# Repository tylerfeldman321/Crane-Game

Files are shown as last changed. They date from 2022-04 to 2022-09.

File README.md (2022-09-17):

<p align="center">
  
</p>

# Advanced Computer Architecture (ECE 350) Project - Crane Game
## Project Description
This is a project a partner and I built for an advanced computer architecture course. We incorporated a custom processor into a physical system we built to create a crane game where the user picks up boxes and drops them into a container to gain points. Our processor keeps track of the score and game logic while the rest of the system handles motors and sensors.

<p align="center">
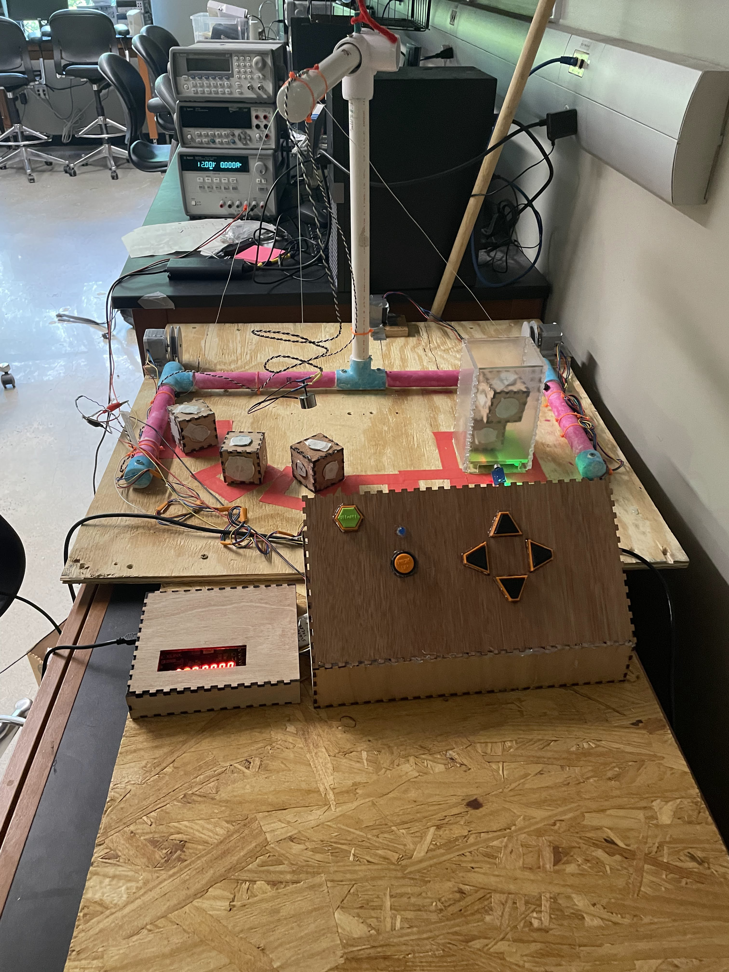
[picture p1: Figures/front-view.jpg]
  
</p>

## Game
The goal of the game is to pickup as many boxes from the playing field and drop them into a acrylic case before time runs out. Once the user presses the start button, time will start counting down from a amount configured in the code (1 minute as default). When the game is active, the user can use the controls to rotate a PVC crane left or right, and move an electromagnet up/down that is hanging off the boom of the crane. The user can click a button to toggle the electromagnet, allowing the crane to pick up the boxes in the playing field. They can then drop them into the acrylic case, gaining points. After the time runs out, the points are recorded and game stops.

Below is a birds-eye view of the game and playing area. The boxes are outlined with red tape, as is the acrylic case on the left, where the user is meant to drop the boxes.

<p align="center">
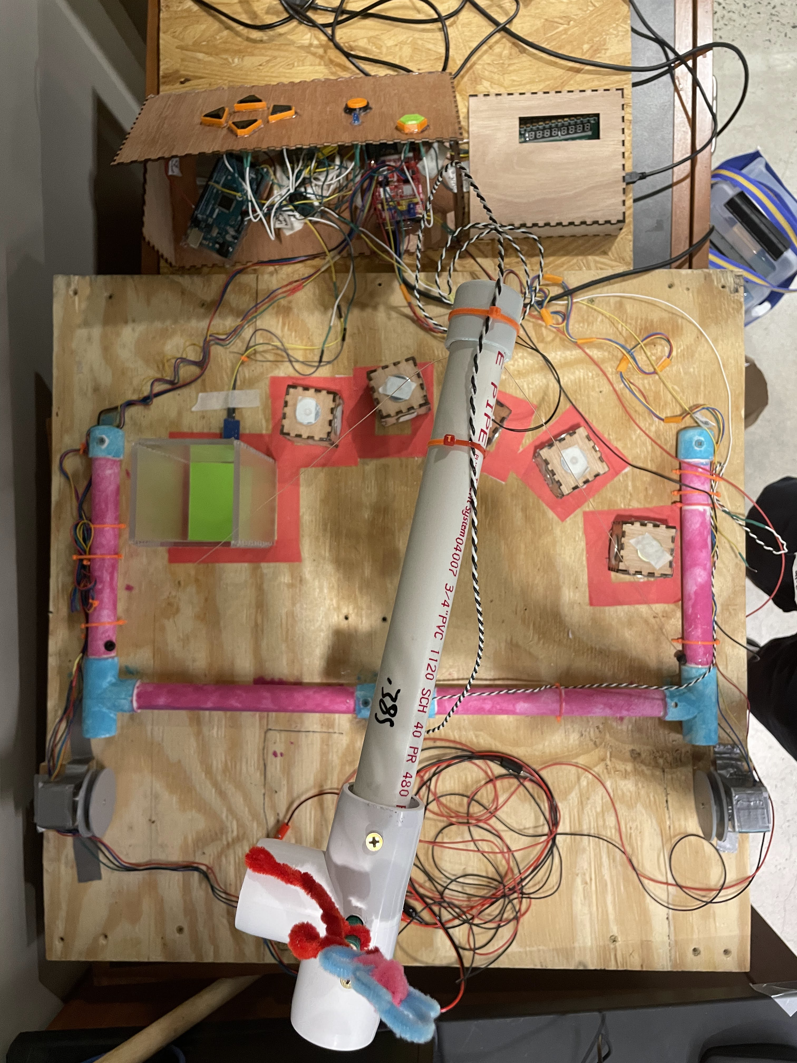
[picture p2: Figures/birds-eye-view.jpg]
  
</p>

## Design
### Mechanical Design
#### Crane
The crane was built out of PVC and built so that the boom of the crane (the horizontal section at the top) could rotate freely. By attaching fishing wire on either side of the end of the boom, we could rotate the crane's boom by pulling on one string and providing slack in the other. To pull / provide slack to the wire, we used a stepper motor on either side that each had wheels that could wind / unwind the wire on that side. When one motor winds the wire and the other unwinds the wire, the crane's boom will be rotated in one direction. Reversing this would cause the crane's boom to rotate in the other direction.

<p align="center">
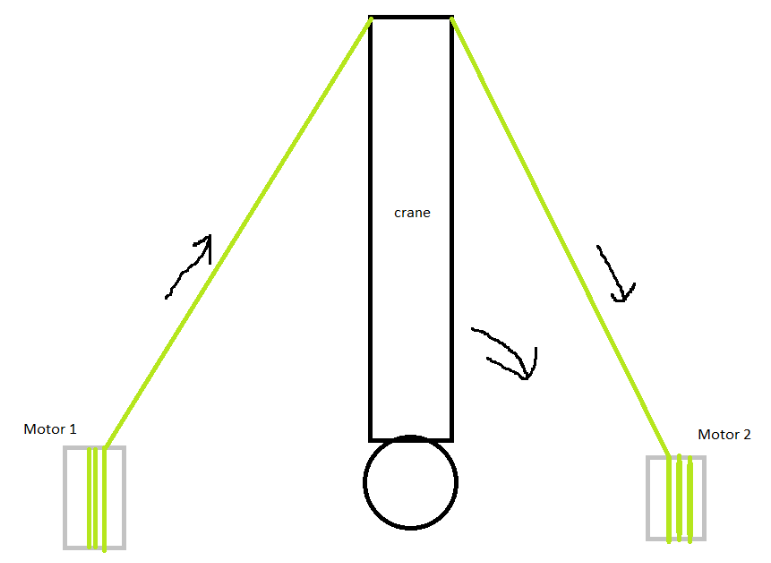
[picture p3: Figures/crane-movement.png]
  
</p>

There is also a third stepper motor placed behind the crane, which winds / unwinds a piece of fishing that runs through the boom of the crane and connects to the hanging electromagnet. When the fishing wire is wound, the electromagnet moves upwards, and when the wire is unwound, the electromagnet moves downwards.

#### Winding Wheel
We designed custom wheels that were spun by our stepper motors so that the fishing wire attached to the end of the boom of the crane could be efficiently wound up. We designed wheels that could fit the shaft of the stepper motors and provide a rod where the fishing wire could be tied and hot glued to. The wheels were also designed with a large enough radius so that the fishing wire wound wind fast enough. They were also designed with a large lip to prevent the fishing wire from slipping out of the wheel when winding or unwinding.

<p align="center">
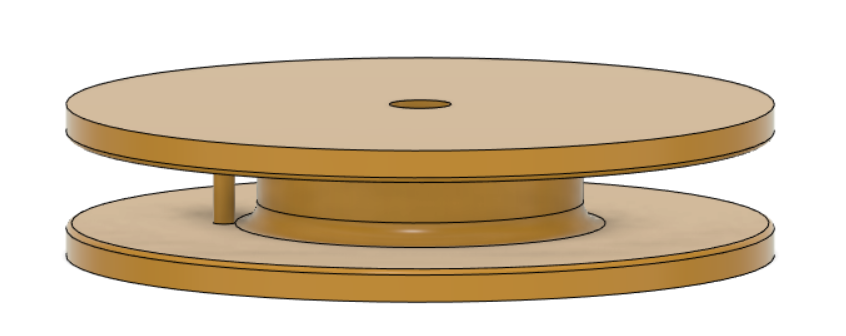
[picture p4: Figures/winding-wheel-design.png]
  
</p>

#### Control Panel
Our control panel was designed to be visually clean and appealing for the user. To do this, we wanted to use panel-mount buttons. We found some viable options for purchase but for full customizability, it made sense to 3D print the buttons. Each button had a outer casing and a inner piece that would fit inside. The outer casing would provide enough room for a common button to be placed at the bottom. When the inner piece is pressed by the user, it would click the button inside as well. The buttons were placed the casing before being hot glued and soldering the connections. Below you can see the design for the start button (left), the front of the control panel when the relay is turned on (middle), and the back of the control panel (right).

<p align="center">
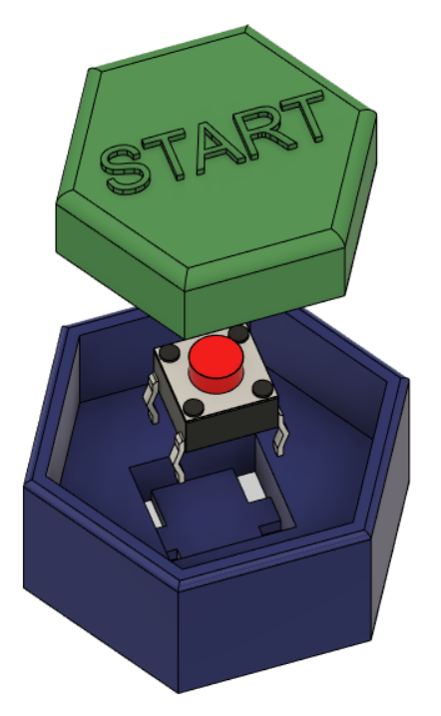
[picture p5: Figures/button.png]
  
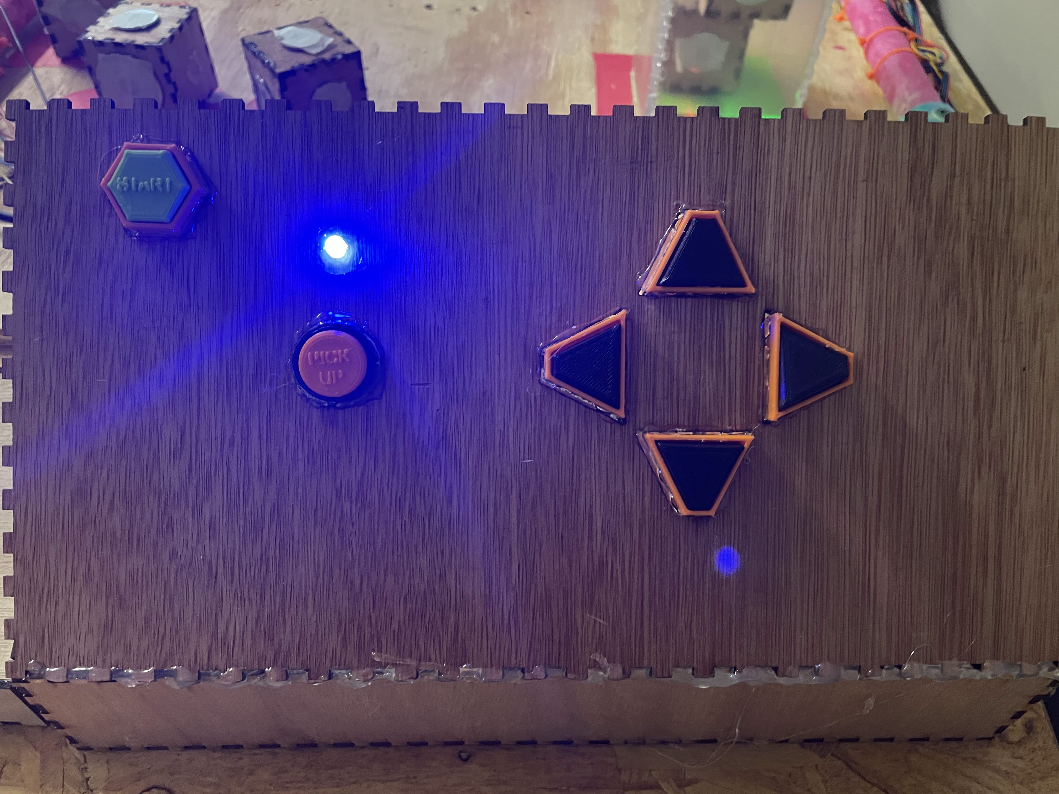
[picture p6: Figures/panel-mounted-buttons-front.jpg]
  
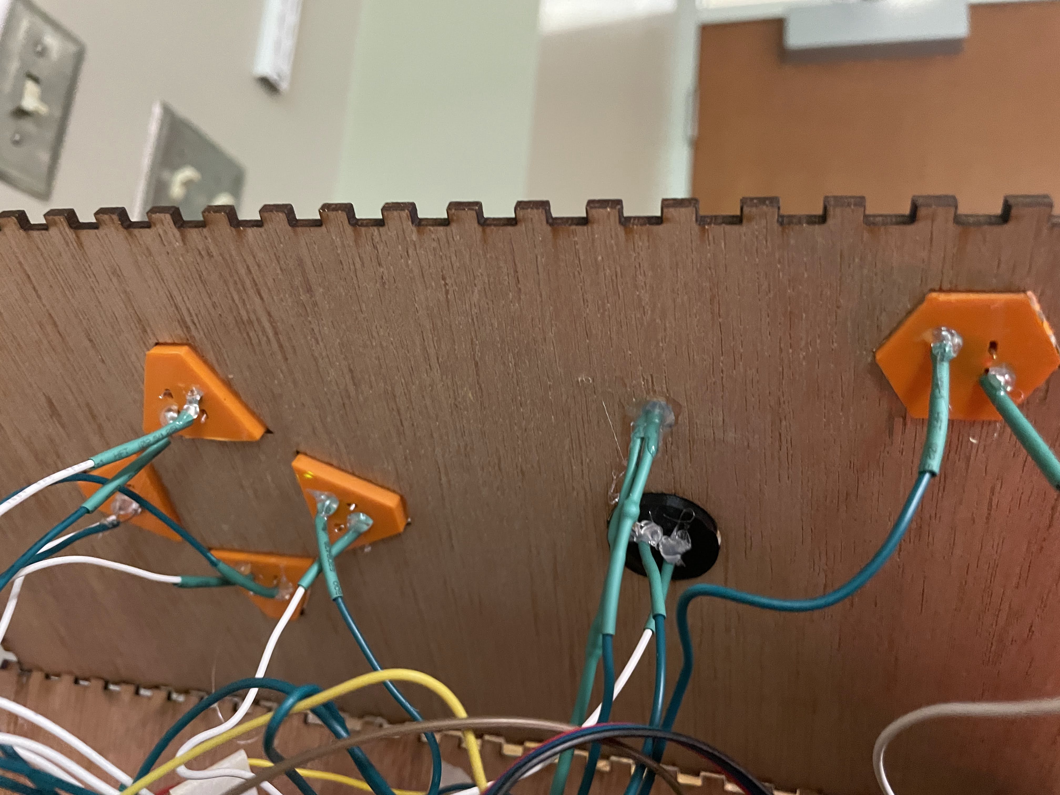
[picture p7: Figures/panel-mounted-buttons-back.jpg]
  
</p>

The control panel was laser cut using thin wood and then glued together after fitting the pieces together. Because our wires and electronics took a lot of space, we weren't able to close the control panel and fit everything in. The control panel and FPGA housing were designed with slots in the sides so that wires could escape out the back or through from the control panel electronics to the FPGA and vice-versa. 

#### Boxes
The boxes were laser cut from wood. To create enough sound so that the sound sensor could easily pick up when a box is dropped in the acrylic case, we put washers inside the boxes. We also hot glued varying-sized washers to the outside of each box so that the electromagnet could pick up each box.

#### Acrylic Case
The acrylic case was laser cut from acrylic. It was designed as a tall rectangular prism with no top or bottom so that boxes could be dropped into it. We also left a slot in the bottom on one of the sides so that the sound sensor or other electronics could make their way inside the case.

<p align="center">
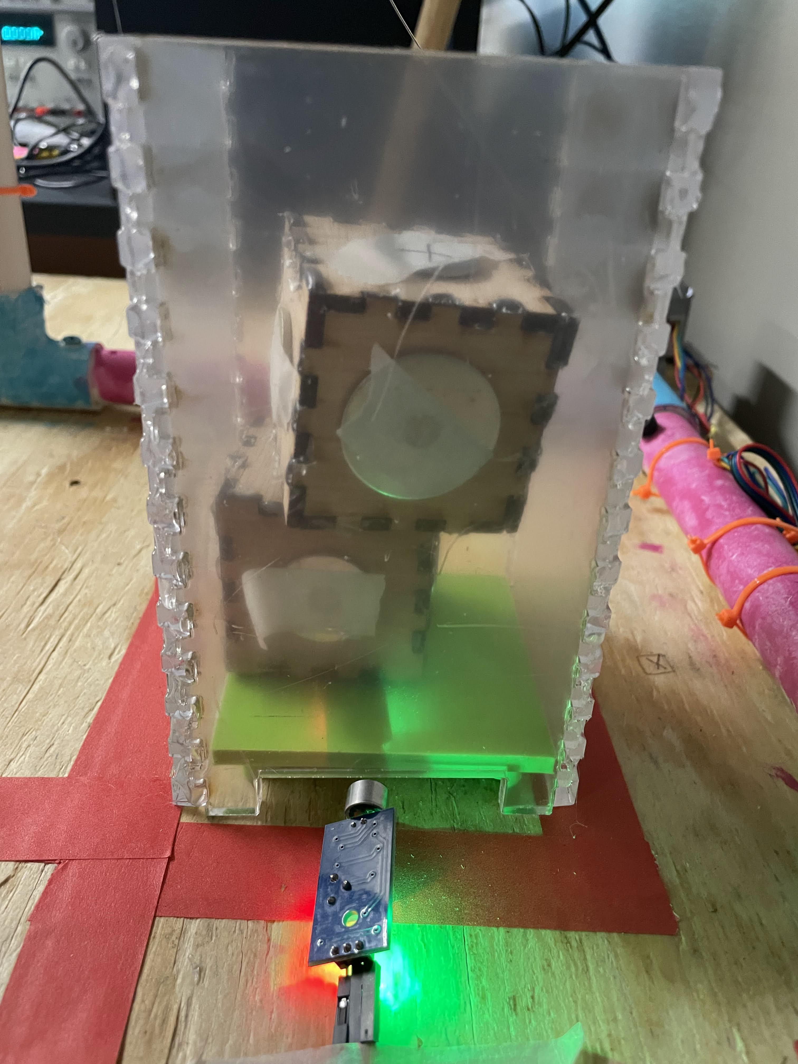
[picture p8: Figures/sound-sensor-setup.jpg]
  
</p>

### Electrical Design
Our electrical system consisted of:
- An arduino to control the stepper motors
- Stepper motor arduino shield attached to the arduino to simplify the control and wiring of multiple stepper motors
- 12 V power suppy for the stepper motors
- Three stepper motors
- An arduino to handle toggling the electromagnet via the relay and handle input from the sound sensor. This arduino would tell the FPGA to increment the score when there were spikes in the sound sensor data.
- Sound sensor
- Relay to electronically control the electromagnet
- LED to signal to the user whether the electromagnet is turned on
- FPGA to handle game logic and send/recieve control signals
- 5V to 3.3V voltage divider to convert signals from the 5V arduino signals to 3.3V for the FPGA

Below are pictures of the electrical system in the control panel and the connections from these electronics to the FPGA.
<p align="center">
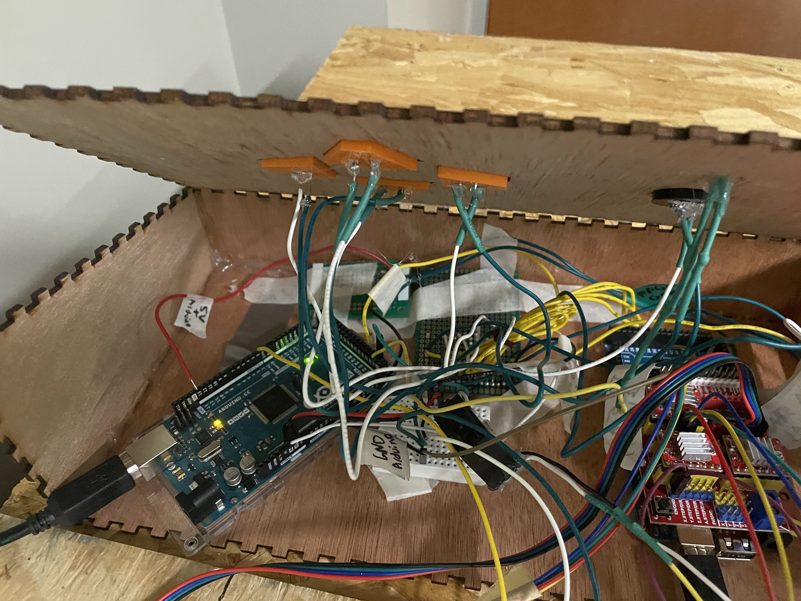
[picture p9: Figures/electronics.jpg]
  
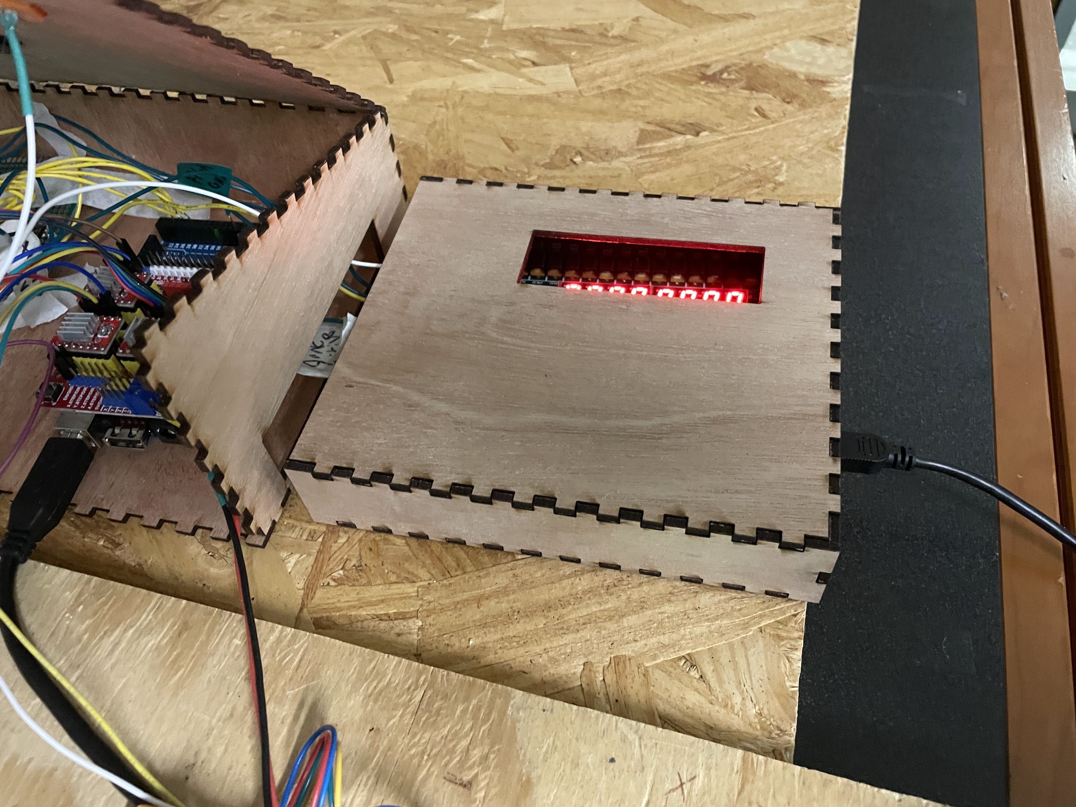
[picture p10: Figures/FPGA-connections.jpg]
  
</p>

#### Electrical Diagram for Entire System
<p align="center">
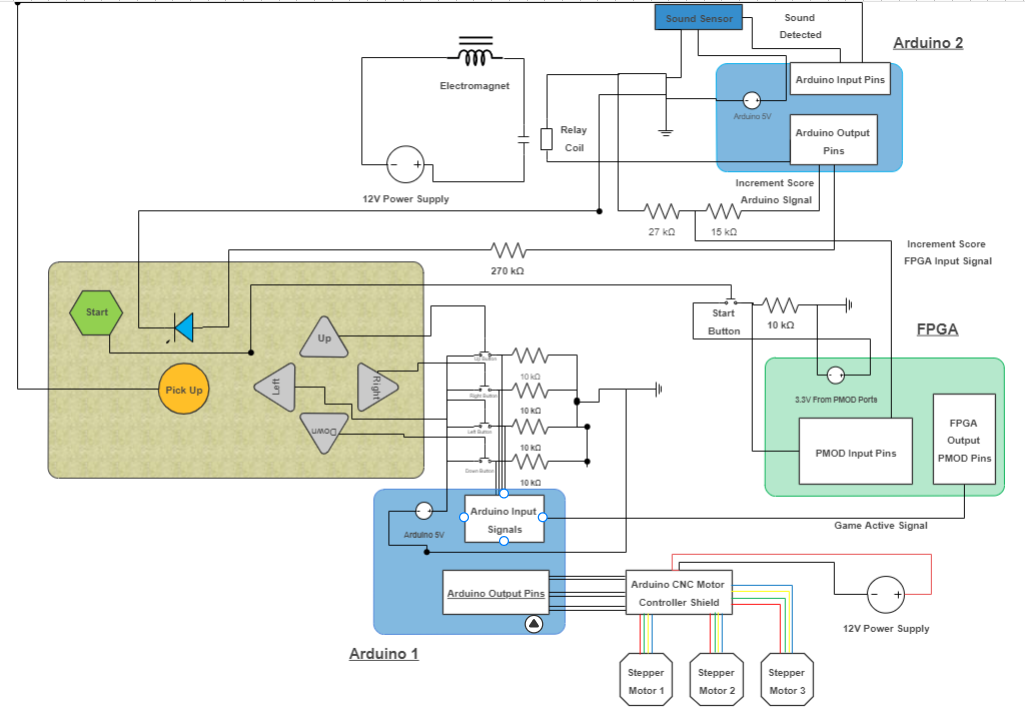
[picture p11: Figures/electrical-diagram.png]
  
</p>

#### Complication with Relay
After soldering all of our components together, we realized that our relay system was not electrically isolated from the rest of the system. Because of this, when we would activate the relay, a voltage spike would occur, causing other signals, like the one to increment the score, to fluctuate. Rather than rewiring / resoldering our connections to isolate the relay, we found a solution through our processor design. By debouncing the input signals to the FPGA, we were able to ignore sudden spikes in the input signals, such as when the relay is toggled.

### Software Design
Our main assembly script for the game logic worked as an event-based program. When particular input signals were recieved by the FPGA, the code would jump to a particular section to handle whatever event occured. It simply consisted of initializing our variables, and then incrementing the score and decrementing the timer when necessary.

<p align="center">
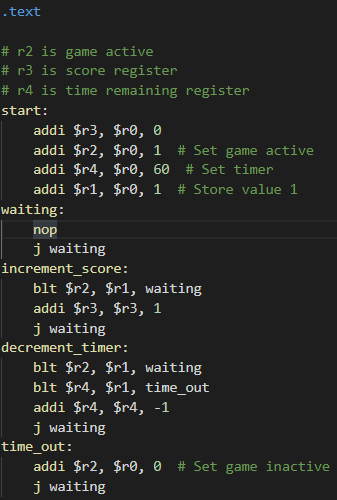
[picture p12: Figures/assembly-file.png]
  
</p>

To accomodate this event-based system, we had to add in interrupt signals into our processor design. When one of these signals was high, then the assembly program would jump directly to the assembly code section to handle the corresponding event, such as when the score needs to be incremented.

We also had arduino code to control the motors, receive and filter input from the sound sensor, and to control the relay. Most of this code was making decisions based on the inputs from the buttons on the control panel. The stepper motor controller code was quite simple since we used the AccelStepper library.

## Design Journey
We had initially decided on the idea of creating a game built like a claw machine (but with an electromagnet instead of a claw), where there is a claw able to be translated in all three directions. This mechanical system is fairly similar to a 3D printer. We also looked into alterante motor / belt configurations like CoreXY as we designed the system. When we finally began prototyping after our parts arrived, we found out that this system is much more difficult to construct that we believed. The precision in our measurements and the calibration of the belts and entire system would have to be perfect or else the system could fail or break. We also realized that the precision movement that this system offered isn't necessary for a game - as long as the user can control generally where the claw goes, they'll have a fun or at least a not-frustrating time playing the game.

That led us to start prototyping and brainstorming new solutions. We landed on two potential solutions: 1) creating a 2D system where a gantry would move along a linear V-slot rail and the electromagnet could be moved up and down, and 2) a crane system where the crane could be rotated left or right. We settled on the crane system as our primary option, and built a very rudamentary initial prototype seen below. The strings could be wound to pull the end of the crane's boom in either direction to rotate it.

<p align="center">
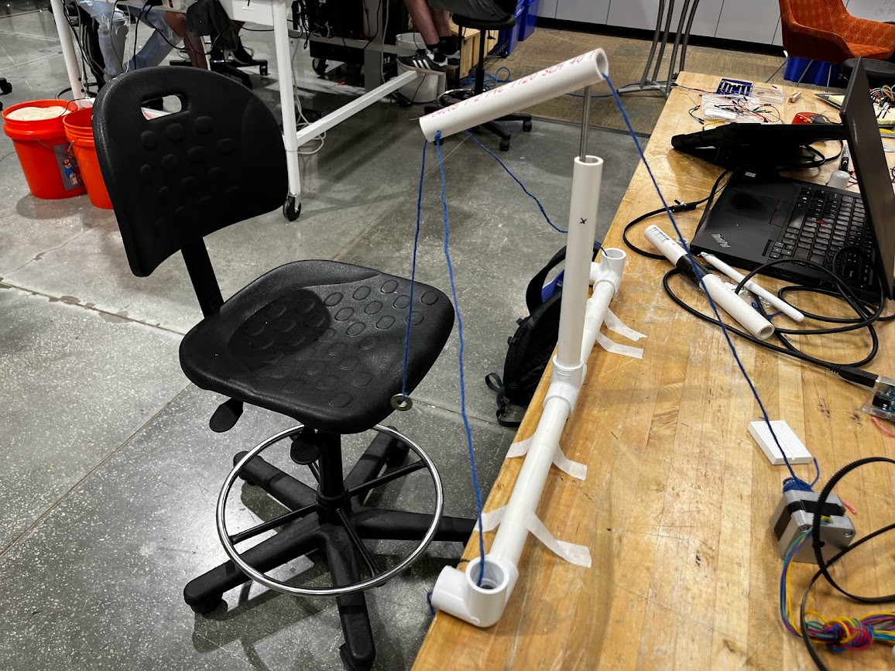
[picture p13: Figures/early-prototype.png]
  
</p>

Our next prototype involved taping some stepper motors down, using winding wheels to wind up fishing wire connected to the boom of the crane, and using a breadboard for our electrical system to control the stepper motors.

<p align="center">
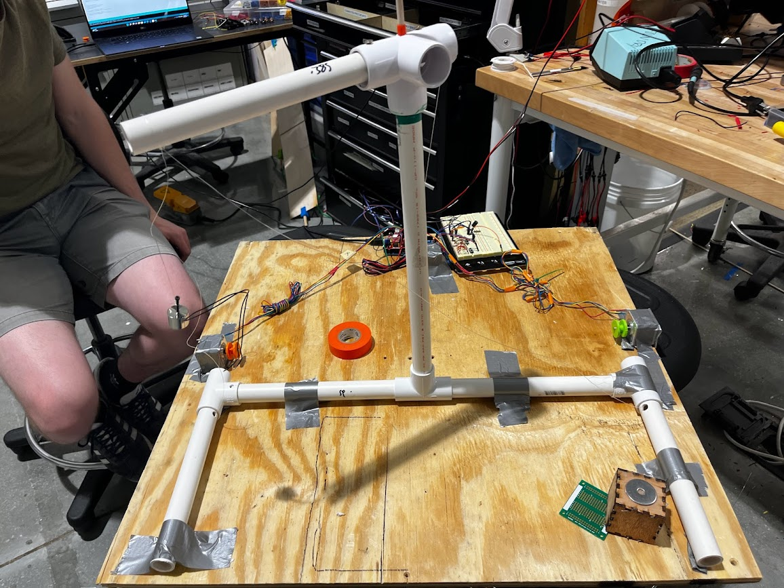
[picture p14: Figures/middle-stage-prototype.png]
  
</p>

We then moved onto more advanced prototypes and continued fabricating the different parts of the game. For score keeping, we had initially planned to use force sensors glued to the bottom of a plate. When the boxes would land on the plate, the force sensors would pick this up and the score would be increased. However, these force sensors kept breaking and were often inconsistent with their measurements. We found a spare sound sensor lying around and decided to use this instead. By filling the boxes with washers, they would make a loud clattering noise when dropped, which could be easily picked up by the sound sensor while filtering out any normal-volume noises.

We learned that, especially for mechanical systems like this, prototyping is extremely important. It should be done alongside brainstorming and designing, rather than spending time designing a system only to find out that it doesn't actually work.

# Processor Design
## Description of Design
The processor I built is a 5-stage pipelined processor. The processor is based on five stages: fetch, decode, execute, memory, and writeback. Between each stage is a latch that remembers the important information for the instruction. This information is passed from latch to latch at each clock cycle, so each stage is finished in one clock cycle. This means that once we have run enough instructions, there will be an instruction completed each clock cycle (assuming they don't involve multi-cycle operations like multiplication and division). 

In fetch, the instruction is read from RAM and the next PC is set. The decode stage is where the instruction reads the registers from the regfile. In execute, the alu is used to compute a result. This result could be a subtraction to determine if a branch should be taken or might be a simple add instruction. In the memory stage, for load word and store word instructions, they either read or write to memory. In writeback, the instructions that write to a register will do so.

## Bypassing
There are various levels of bypassing, including jump register, bypassing to the memory stage, and bypassing to the A and B operands in the execute stage. The bypassing is done from stages ahead of each particular stage. There is also priority involved with all of the bypassing in my processor,, which favors the closest instruction. For example, if an instruction in execute is reading from register 1 but there instructions in both memory and writeback that are writing to register 1, the result from the instruction in memory should be bypassed. It was also important to check that both the write enable of the instruction to bypass from is on, and also that the instruction to bypass from is not writing to register 0, since that will always stay 0.

The first level of bypassing is for the jump register instruction. This instruction is able to be executed during the decode stage, and reads from a particular register. This means that if an instruction in the execute, memory, or writeback stage is writing to the register that the JR is going to read from, bypassing is necessary.

There is bypassing from memory and writeback to the A and B register values in the execute stage. This was done by checking if the instructions in memory or writeback were going to write to a register that the instruction in execute has ready already. 

There is also bypassing to memory from writeback for the data that will be written into memory.

## Stalling
In the case that bypassing cannot handle a data hazard, stalling is used. Stalling consists of writing nops into the DX register, clearing all the datapath control signals, and disabling the FD latch and PC register. This allows the problematic instruction to run and move to the next cycle, while keeping the dependent instructions in the same location. Once the instructions are separated enough, then the pipeline can resume fetching instructions. The stalling is done only for the case of a lw instruction in execute and an instruction that will read it's result in the decode stage.

I also used stalling to complete the multiplication and division operations. Because of complexities with writing the registers and stalling on any instruction that reads or writes to the result register for multiplication or division, I decided to stall the processor while multiplication or division was running.

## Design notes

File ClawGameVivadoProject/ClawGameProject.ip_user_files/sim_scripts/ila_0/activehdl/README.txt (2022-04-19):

################################################################################
# Vivado (TM) v2020.1 (64-bit)
#
# README.txt: Please read the sections below to understand the steps required to
#             run the exported script and information about the source files.
#
# Generated by export_simulation on Tue Apr 19 01:52:37 -0400 2022
#
################################################################################

1. How to run the generated simulation script:-

From the shell prompt in the current directory, issue the following command:-

./ila_0.sh

This command will launch the 'compile', 'elaborate' and 'simulate' functions
implemented in the script file for the 3-step flow. These functions are called
from the main 'run' function in the script file.

The 'run' function first executes the 'setup' function, the purpose of which is to
create simulator specific setup files, create design library mappings and library
directories and copy 'glbl.v' from the Vivado software install location into the
current directory.

The 'setup' function is also used for removing the simulator generated data in
order to reset the current directory to the original state when export_simulation
was launched from Vivado. This generated data can be removed by specifying the
'-reset_run' switch to the './ila_0.sh' script.

./ila_0.sh -reset_run

To keep the generated data from the previous run but regenerate the setup files and
library directories, use the '-noclean_files' switch.

./ila_0.sh -noclean_files

For more information on the script, please type './ila_0.sh -help'.

2. Additional design information files:-

export_simulation generates following additional file that can be used for fetching
the design files information or for integrating with external custom scripts.

Name   : file_info.txt
Purpose: This file contains detail design file information based on the compile order
         when export_simulation was executed from Vivado. The file contains information
         about the file type, name, whether it is part of the IP, associated library
         and the file path information.

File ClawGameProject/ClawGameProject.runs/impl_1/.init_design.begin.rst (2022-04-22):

<?xml version="1.0"?>
<ProcessHandle Version="1" Minor="0">
    <Process Command=".planAhead." Owner="tyler" Host="DESKTOP-IOM2HT6" Pid="34608">
    </Process>
</ProcessHandle>

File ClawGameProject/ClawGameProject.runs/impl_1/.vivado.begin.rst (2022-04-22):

<?xml version="1.0"?>
<ProcessHandle Version="1" Minor="0">
    <Process Command="vivado.bat" Owner="tyler" Host="DESKTOP-IOM2HT6" Pid="36736" HostCore="12" HostMemory="016946126848">
    </Process>
</ProcessHandle>

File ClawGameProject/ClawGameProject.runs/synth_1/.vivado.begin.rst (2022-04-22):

<?xml version="1.0"?>
<ProcessHandle Version="1" Minor="0">
    <Process Command="vivado.bat" Owner="tyler" Host="DESKTOP-IOM2HT6" Pid="35048" HostCore="12" HostMemory="016946126848">
    </Process>
</ProcessHandle>

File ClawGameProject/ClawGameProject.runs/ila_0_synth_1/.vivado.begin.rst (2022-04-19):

<?xml version="1.0"?>
<ProcessHandle Version="1" Minor="0">
    <Process Command="vivado.bat" Owner="tyler" Host="DESKTOP-IOM2HT6" Pid="17748" HostCore="12" HostMemory="016946126848">
    </Process>
</ProcessHandle>

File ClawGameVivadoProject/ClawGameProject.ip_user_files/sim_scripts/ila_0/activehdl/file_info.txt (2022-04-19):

xpm_cdc.sv,systemverilog,xpm,../../../../../../../../../Xilinx/Vivado/2020.1/data/ip/xpm/xpm_cdc/hdl/xpm_cdc.sv,incdir="../../../../ClawGameProject.srcs/sources_1/ip/ila_0/hdl/verilog"
xpm_memory.sv,systemverilog,xpm,../../../../../../../../../Xilinx/Vivado/2020.1/data/ip/xpm/xpm_memory/hdl/xpm_memory.sv,incdir="../../../../ClawGameProject.srcs/sources_1/ip/ila_0/hdl/verilog"
xpm_VCOMP.vhd,vhdl,xpm,../../../../../../../../../Xilinx/Vivado/2020.1/data/ip/xpm/xpm_VCOMP.vhd,incdir="../../../../ClawGameProject.srcs/sources_1/ip/ila_0/hdl/verilog"
ila_0.v,verilog,xil_defaultlib,../../../../ClawGameProject.srcs/sources_1/ip/ila_0/sim/ila_0.v,incdir="../../../../ClawGameProject.srcs/sources_1/ip/ila_0/hdl/verilog"
glbl.v,Verilog,xil_defaultlib,glbl.v

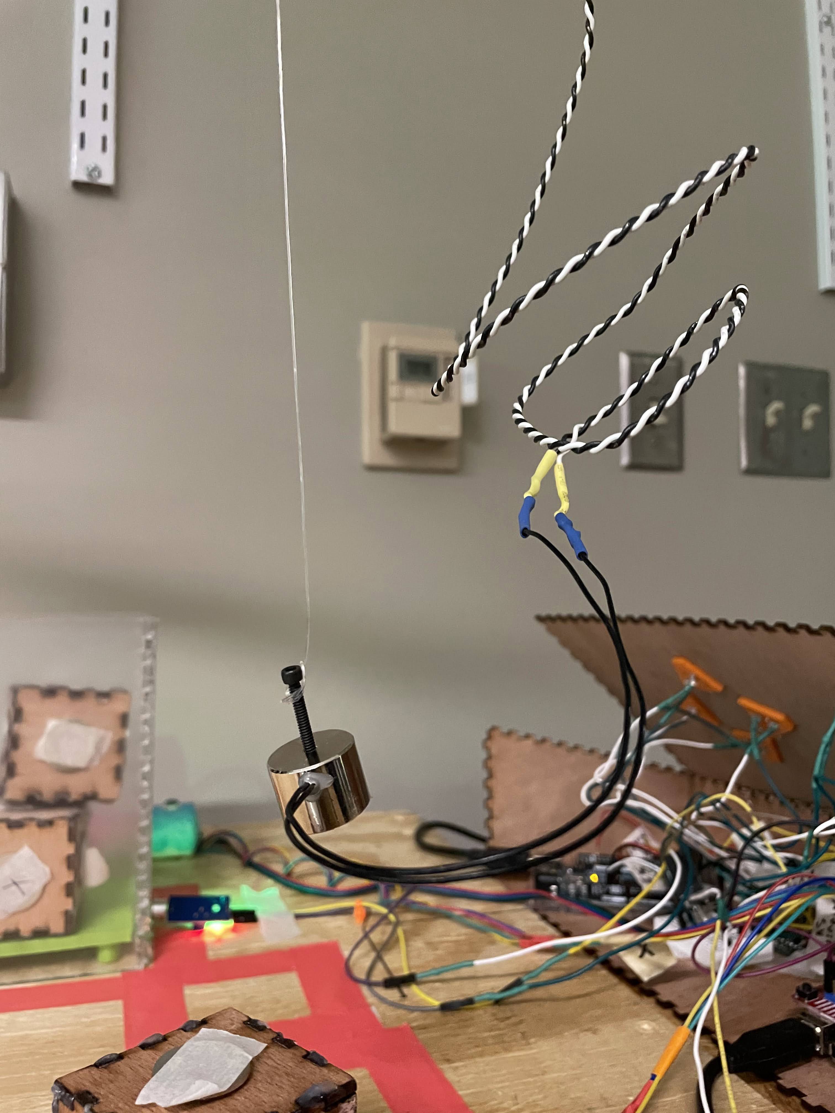
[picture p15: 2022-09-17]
Figures/electromagnet.jpg

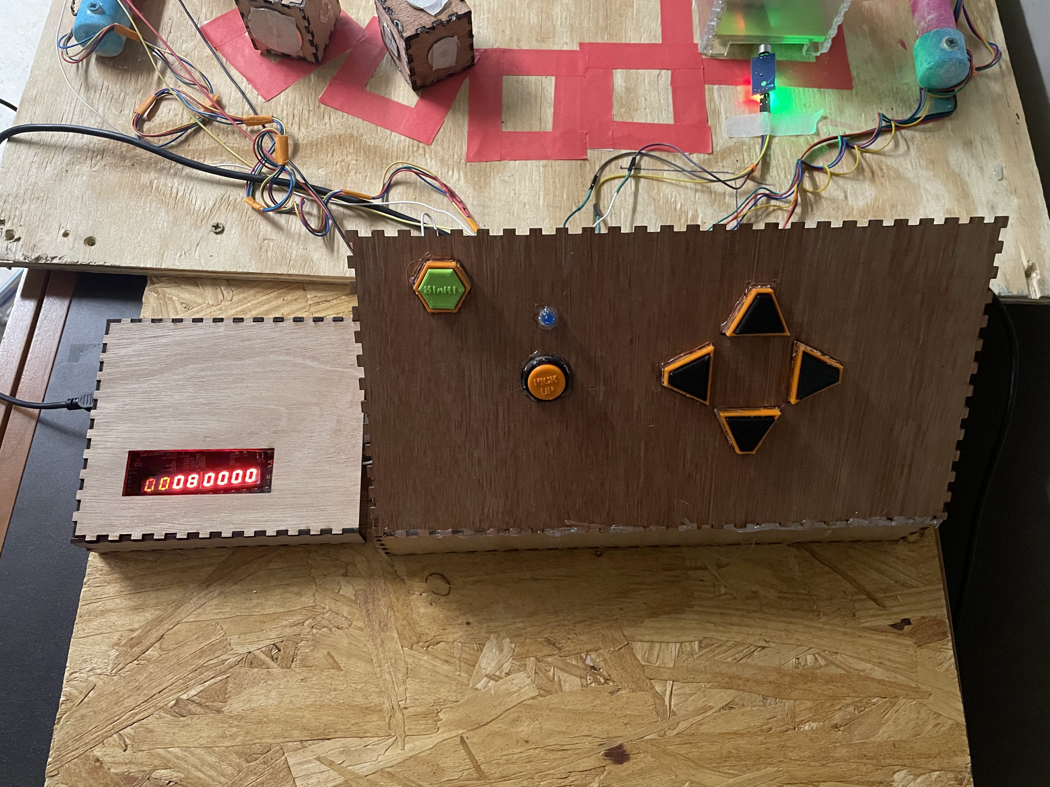
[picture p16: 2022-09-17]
Figures/user-interface.jpg

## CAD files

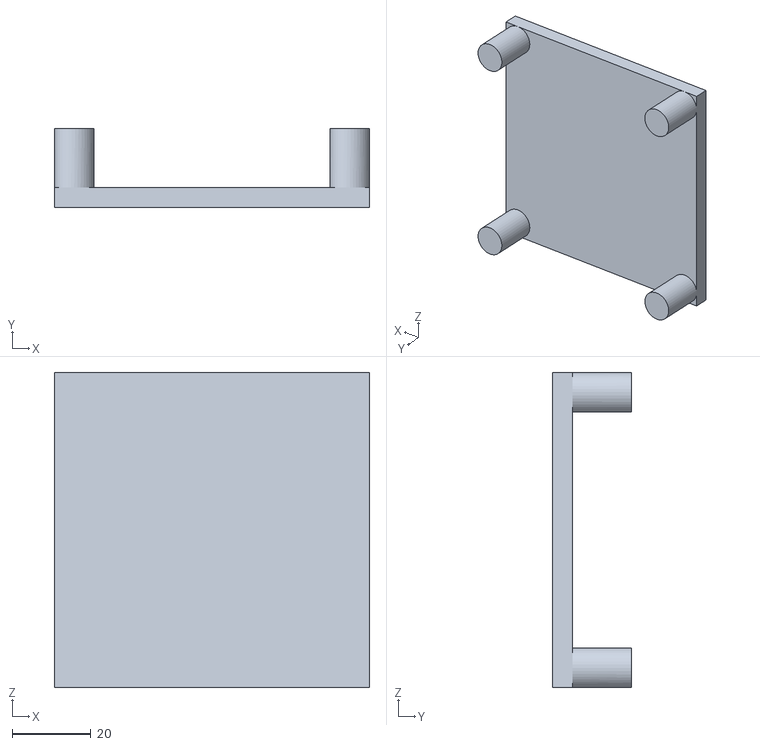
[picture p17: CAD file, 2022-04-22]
3D Models/Load Plate v9.stl
80.0 x 20.0 x 80.0

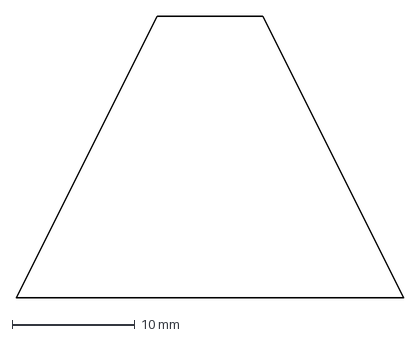
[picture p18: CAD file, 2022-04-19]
Laser Cutting Files/Triangle Button 0.5 offset.dxf
31.6 x 23.0 mm

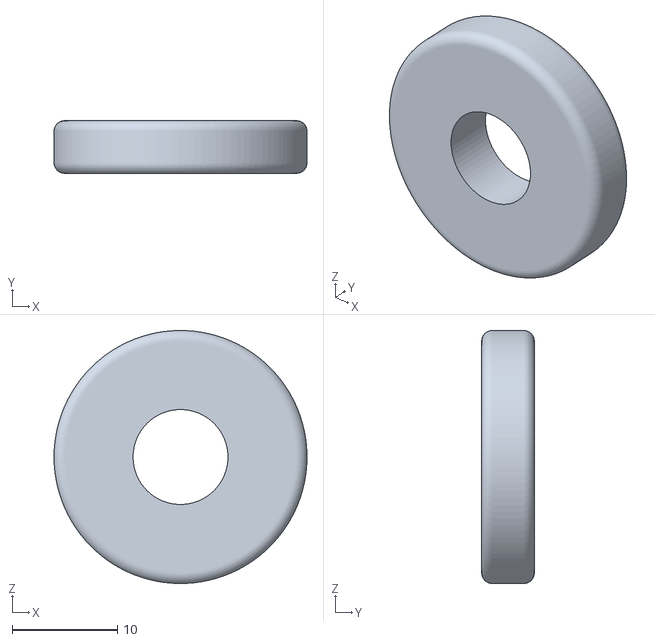
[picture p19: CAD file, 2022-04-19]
3D Models/Basic Wheel v6.stl
24.0 x 5.00 x 24.0

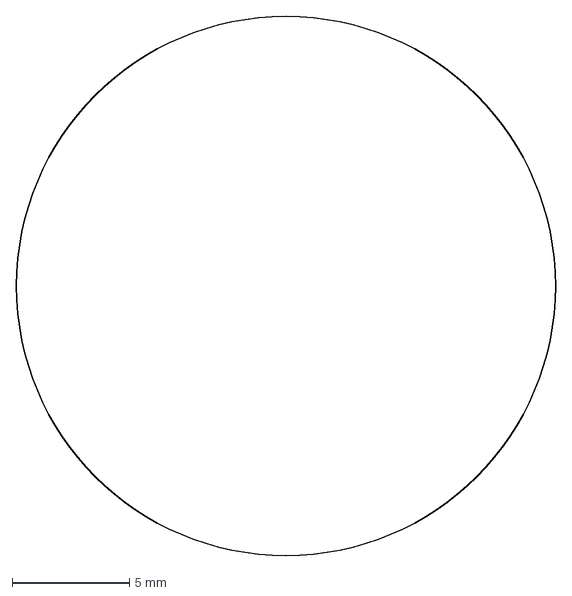
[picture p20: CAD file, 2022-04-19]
Laser Cutting Files/Circle Button 0.5 offset.dxf
23.0 x 23.0 mm

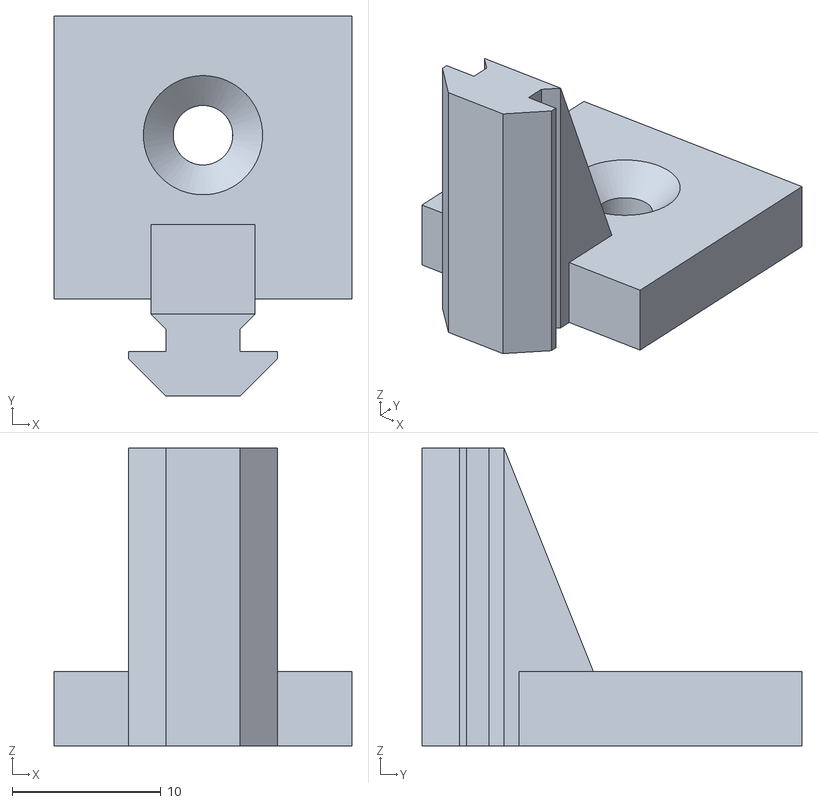
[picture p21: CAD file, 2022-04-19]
3D Models/V Slot Wood Mount v5.stl
20.0 x 25.5 x 20.0

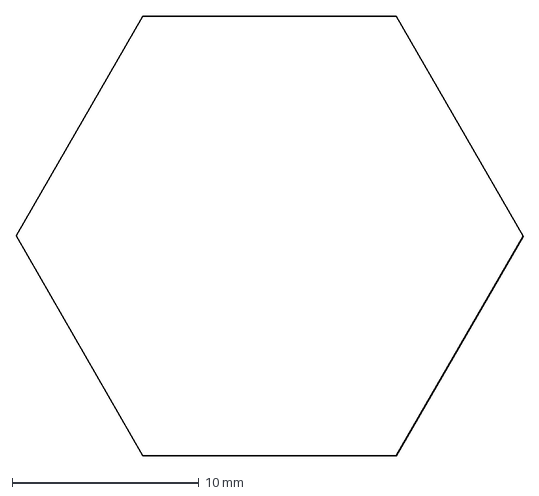
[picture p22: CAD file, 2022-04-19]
Laser Cutting Files/Start Button 0.5 offset.dxf
27.2 x 23.5 mm

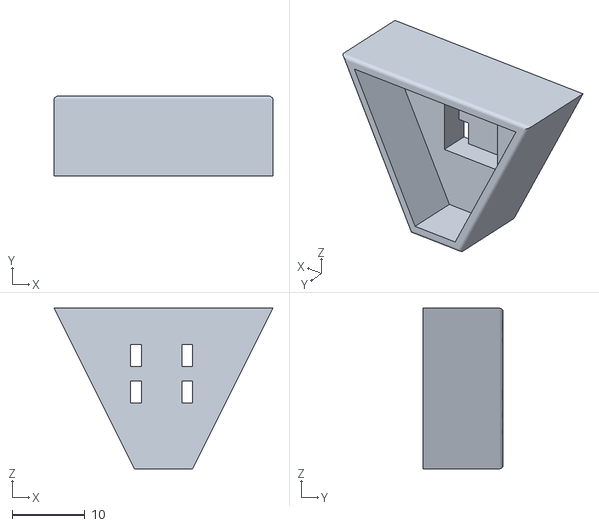
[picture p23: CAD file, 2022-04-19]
3D Models/Game Button Triangle v9 Outer.stl
30.0 x 11.0 x 22.0

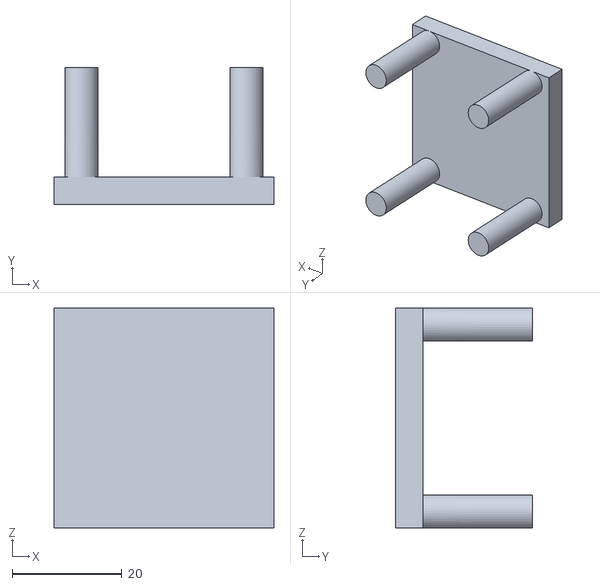
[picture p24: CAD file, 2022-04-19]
3D Models/Cart v1.stl
40.0 x 25.0 x 40.0

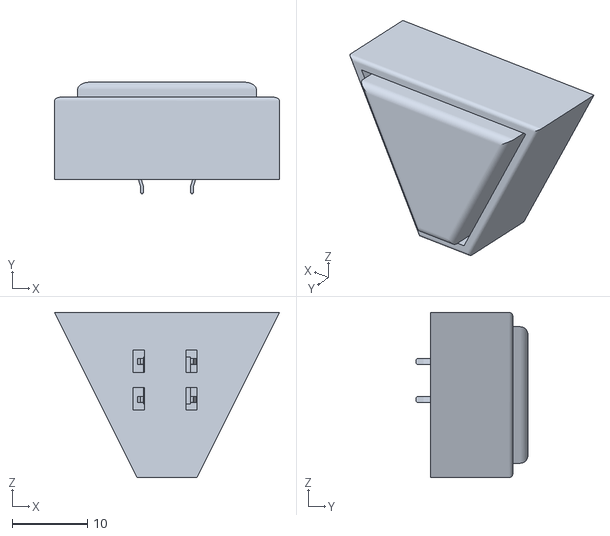
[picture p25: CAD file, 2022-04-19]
3D Models/Game Button Triangle v9.stl
30.0 x 14.9 x 22.0

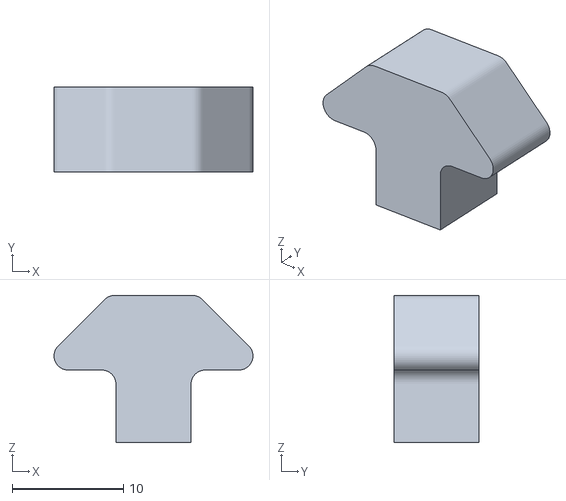
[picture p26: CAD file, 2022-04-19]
3D Models/V-Slot Linear Rail Rod Mount v2.stl
17.9 x 7.62 x 13.2

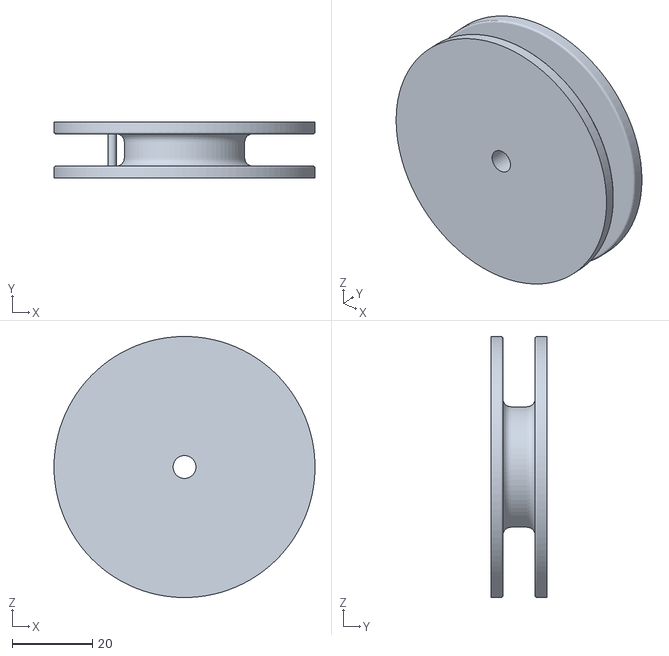
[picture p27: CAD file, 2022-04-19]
3D Models/Winding Gear Circular Motor Shaft v5.stl
65.0 x 14.0 x 65.0

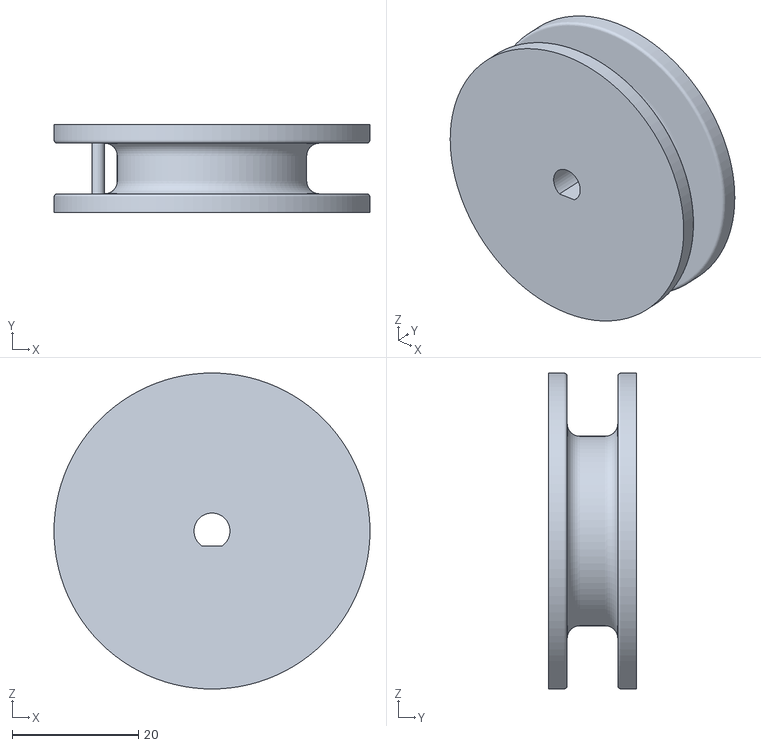
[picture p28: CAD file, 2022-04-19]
3D Models/Winding Gear v10.stl
50.0 x 14.0 x 50.0

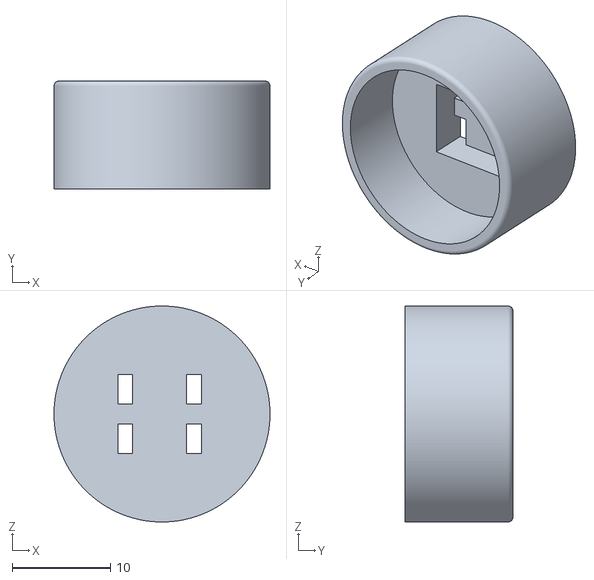
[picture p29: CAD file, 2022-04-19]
3D Models/Game Button Pick Up Outer.stl
22.0 x 11.0 x 22.0

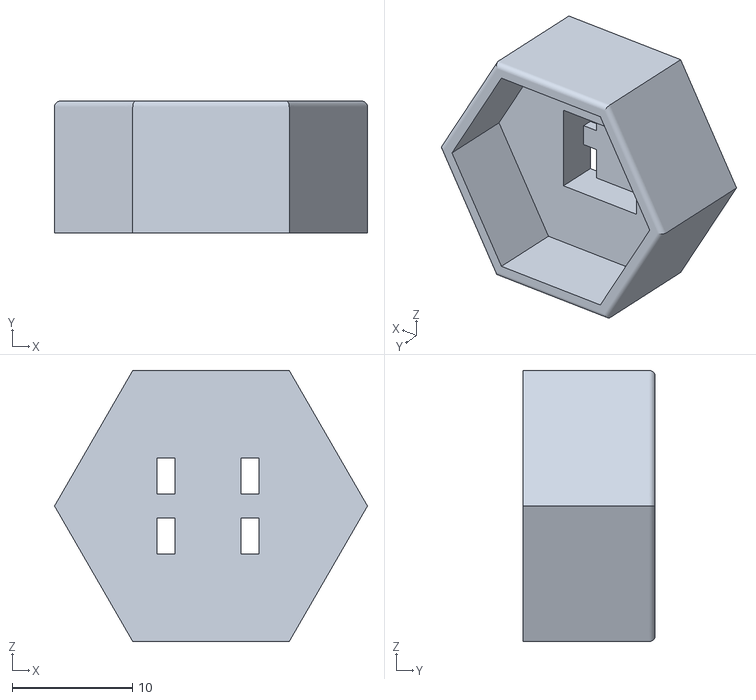
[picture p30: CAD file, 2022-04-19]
3D Models/Game Button Start v3 Outer.stl
26.0 x 11.0 x 22.5

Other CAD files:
3D Models/Load Plate v7 - smaller.stl
3D Models/Carriage v5.stl
3D Models/Game Button Triangle v9 Inner.stl
3D Models/Game Button Inner v2.stl
3D Models/Basic Wheel v1.stl
3D Models/Basic Wheel v2.stl
3D Models/Basic Wheel v3.stl
3D Models/Basic Wheel v5.stl
3D Models/Carriage v3.stl
3D Models/Carriage v4.stl
3D Models/Game Button Outer v2.stl
3D Models/Game Button Pick Up Inner.stl
3D Models/Game Button Start v1 Inner.stl
3D Models/Game Button Start v1 Outer.stl
3D Models/Game Button Start v3 Inner.stl
3D Models/Load Plate v1.stl
3D Models/Load Plate v2.stl
3D Models/Load Plate v3.stl
3D Models/Load Plate v4.f3d
3D Models/Load Plate v4.stl
3D Models/Load Plate v5.stl
3D Models/Load Plate v6 - 5 pegs.stl
3D Models/Load Plate v8 - smaller and cone legs.stl
3D Models/V Slot Wood Mount v3.stl
3D Models/V Slot Wood Mount v4.stl
3D Models/V-Slot Linear Rail Rod Mount v1.stl
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

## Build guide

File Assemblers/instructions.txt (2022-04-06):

This program can assemble ECE350 limited-ISA MIPS assembly into machine code. 

== Choosing which executable to use
We have compiled the assembler for all of the major operating systems for you to use. You can move the compiled file from the operating system folder into the top assembler folder.

You can move the file using the Finder or File Explorer applications on your computer or use the command line.

For example: 
If you are using a windows computer, move the file from ./windows/asm to ./asm

If you are using a Mac made after 2020, you can use the cp command to move the assembler using the following command:

	cp ./mac_m1/asm ./ 

== Using the program

asm [flags] <filename>

Args:
<filename>  name of the assembly file to assemble

Optional Flags:
-o      name of the output file
-i      csv file containing custom instruction definitions
-r      csv file containing custom register aliases
-b      output base of instructions (only 2 or 16 supported). Defaults to binary.
-l      number of 32-bit words in output file

== Custom Instructions

Custom instructions should be defined in a .csv file. Each row specifies a single instruction 
and should match the following format: instruction, type, opcode.

For example:

print,J,11000
draw,R,11001

== Custom Register Aliases

You can define additional register aliases in another .csv file. The first column of the row
defines which register to assign aliases and following columns are all assigned as aliases.

For example:
2,sprite
3,reg3
3,register3
3,three

This will set "sprite" to be an alias for register 2 and "reg3", "register3", and "three"
to be aliases for register 3. Then these aliases can be used in the assembly files in place of the
register number.

add $three, $sprite, $reg3 <==> add $3, $2, $3

== author Jack Proudfoot

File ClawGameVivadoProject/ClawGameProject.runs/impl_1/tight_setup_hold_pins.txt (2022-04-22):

+--------------------------+--------------------------+----------------------------------------------------------------------------------------------------------+
|       Launch Clock       |      Capture Clock       |                                                 Pin                                                      |
+--------------------------+--------------------------+----------------------------------------------------------------------------------------------------------+
|              sys_clk_pin |              sys_clk_pin |                                                               WRAPPER/CPU/FD_PC_reg/loop1[13].dff/q_reg/D|
|              sys_clk_pin |              sys_clk_pin |                                                               WRAPPER/CPU/FD_PC_reg/loop1[19].dff/q_reg/D|
|              sys_clk_pin |              sys_clk_pin |                                                                WRAPPER/CPU/FD_PC_reg/loop1[3].dff/q_reg/D|
|              sys_clk_pin |              sys_clk_pin |                                                                WRAPPER/CPU/FD_PC_reg/loop1[4].dff/q_reg/D|
|              sys_clk_pin |              sys_clk_pin |                                                               WRAPPER/CPU/FD_PC_reg/loop1[12].dff/q_reg/D|
|              sys_clk_pin |              sys_clk_pin |                                                                WRAPPER/CPU/FD_PC_reg/loop1[9].dff/q_reg/D|
|              sys_clk_pin |              sys_clk_pin |                                                               WRAPPER/CPU/FD_PC_reg/loop1[10].dff/q_reg/D|
|              sys_clk_pin |              sys_clk_pin |                                                               WRAPPER/CPU/DX_PC_reg/loop1[30].dff/q_reg/D|
|              sys_clk_pin |              sys_clk_pin |                                                               WRAPPER/CPU/FD_PC_reg/loop1[28].dff/q_reg/D|
|              sys_clk_pin |              sys_clk_pin |                                                                WRAPPER/CPU/DX_PC_reg/loop1[3].dff/q_reg/D|
|              sys_clk_pin |              sys_clk_pin |                                                               WRAPPER/CPU/DX_PC_reg/loop1[16].dff/q_reg/D|
|              sys_clk_pin |              sys_clk_pin |                                                               WRAPPER/CPU/FD_PC_reg/loop1[21].dff/q_reg/D|
|              sys_clk_pin |              sys_clk_pin |                                                               WRAPPER/CPU/FD_IR_reg/loop1[31].dff/q_reg/D|
|              sys_clk_pin |              sys_clk_pin |                                                               WRAPPER/CPU/DX_PC_reg/loop1[24].dff/q_reg/D|
|              sys_clk_pin |              sys_clk_pin |                                                                WRAPPER/CPU/DX_PC_reg/loop1[4].dff/q_reg/D|
|              sys_clk_pin |              sys_clk_pin |                                                               WRAPPER/CPU/FD_IR_reg/loop1[29].dff/q_reg/D|
|              sys_clk_pin |              sys_clk_pin |                                                                WRAPPER/CPU/DX_PC_reg/loop1[1].dff/q_reg/D|
|              sys_clk_pin |              sys_clk_pin |                                                               WRAPPER/CPU/DX_IR_reg/loop1[17].dff/q_reg/D|
|              sys_clk_pin |              sys_clk_pin |                                                               WRAPPER/CPU/FD_PC_reg/loop1[23].dff/q_reg/D|
|              sys_clk_pin |              sys_clk_pin |                                                                WRAPPER/CPU/DX_PC_reg/loop1[6].dff/q_reg/D|
|              sys_clk_pin |              sys_clk_pin |                                                               WRAPPER/CPU/DX_PC_reg/loop1[19].dff/q_reg/D|
|              sys_clk_pin |              sys_clk_pin |                                                               WRAPPER/CPU/DX_PC_reg/loop1[20].dff/q_reg/D|
|              sys_clk_pin |              sys_clk_pin |                                                               WRAPPER/CPU/DX_PC_reg/loop1[18].dff/q_reg/D|
|              sys_clk_pin |              sys_clk_pin |                                                               WRAPPER/CPU/FD_IR_reg/loop1[22].dff/q_reg/D|
|              sys_clk_pin |              sys_clk_pin |                                                               WRAPPER/CPU/DX_PC_reg/loop1[11].dff/q_reg/D|
|              sys_clk_pin |              sys_clk_pin |                                                               WRAPPER/CPU/FD_IR_reg/loop1[23].dff/q_reg/D|
|              sys_clk_pin |              sys_clk_pin |                                                               WRAPPER/CPU/FD_PC_reg/loop1[20].dff/q_reg/D|
|              sys_clk_pin |              sys_clk_pin |                                                               WRAPPER/CPU/DX_PC_reg/loop1[14].dff/q_reg/D|
|              sys_clk_pin |              sys_clk_pin |                                                               WRAPPER/CPU/DX_PC_reg/loop1[10].dff/q_reg/D|
|              sys_clk_pin |              sys_clk_pin |                                                               WRAPPER/CPU/DX_IR_reg/loop1[23].dff/q_reg/D|
|              sys_clk_pin |              sys_clk_pin |                                                               WRAPPER/CPU/DX_IR_reg/loop1[18].dff/q_reg/D|
|              sys_clk_pin |              sys_clk_pin |                                                               WRAPPER/CPU/DX_IR_reg/loop1[19].dff/q_reg/D|
|              sys_clk_pin |              sys_clk_pin |                                                                WRAPPER/CPU/DX_IR_reg/loop1[2].dff/q_reg/D|
|              sys_clk_pin |              sys_clk_pin |                                                               WRAPPER/CPU/DX_IR_reg/loop1[22].dff/q_reg/D|
|              sys_clk_pin |              sys_clk_pin |                                                               WRAPPER/CPU/DX_PC_reg/loop1[13].dff/q_reg/D|
|              sys_clk_pin |              sys_clk_pin |                                                                WRAPPER/CPU/DX_IR_reg/loop1[1].dff/q_reg/D|
|              sys_clk_pin |              sys_clk_pin |                                                                WRAPPER/CPU/DX_PC_reg/loop1[2].dff/q_reg/D|
|              sys_clk_pin |              sys_clk_pin |                                                                WRAPPER/CPU/DX_IR_reg/loop1[3].dff/q_reg/D|
|              sys_clk_pin |              sys_clk_pin |                                                               WRAPPER/CPU/DX_PC_reg/loop1[22].dff/q_reg/D|
|              sys_clk_pin |              sys_clk_pin |                                                               WRAPPER/CPU/DX_PC_reg/loop1[21].dff/q_reg/D|
|              sys_clk_pin |              sys_clk_pin |                                                               WRAPPER/CPU/DX_PC_reg/loop1[23].dff/q_reg/D|
|              sys_clk_pin |              sys_clk_pin |                                                                WRAPPER/CPU/DX_PC_reg/loop1[8].dff/q_reg/D|
|              sys_clk_pin |              sys_clk_pin |                                                               WRAPPER/CPU/DX_PC_reg/loop1[25].dff/q_reg/D|
+--------------------------+--------------------------+----------------------------------------------------------------------------------------------------------+

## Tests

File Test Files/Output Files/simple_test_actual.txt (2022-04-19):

Cycle   4: Wrote 1 into register 1
Cycle   5: Wrote 20 into register 10
Cycle   6: Wrote 10000 into register 11
Cycle   7: Wrote 9999 into register 11
Cycle  13: Wrote 9998 into register 11
Cycle  19: Wrote 9997 into register 11
Cycle  25: Wrote 9996 into register 11
Cycle  31: Wrote 9995 into register 11
Cycle  37: Wrote 9994 into register 11
Cycle  43: Wrote 9993 into register 11
Cycle  49: Wrote 9992 into register 11
Cycle  55: Wrote 9991 into register 11
Cycle  61: Wrote 9990 into register 11
Cycle  67: Wrote 9989 into register 11
Cycle  73: Wrote 9988 into register 11
Cycle  79: Wrote 9987 into register 11
Cycle  85: Wrote 9986 into register 11
Cycle  91: Wrote 9985 into register 11
Cycle  97: Wrote 9984 into register 11
Cycle 103: Wrote 9983 into register 11
Cycle 109: Wrote 9982 into register 11
Cycle 115: Wrote 9981 into register 11
Cycle 121: Wrote 9980 into register 11
Cycle 127: Wrote 9979 into register 11
Cycle 133: Wrote 9978 into register 11
Cycle 139: Wrote 9977 into register 11
Cycle 145: Wrote 9976 into register 11
Cycle 151: Wrote 9975 into register 11
Cycle 157: Wrote 9974 into register 11
Cycle 163: Wrote 9973 into register 11
Cycle 169: Wrote 9972 into register 11
Cycle 175: Wrote 9971 into register 11
Cycle 181: Wrote 9970 into register 11
Cycle 187: Wrote 9969 into register 11
Cycle 193: Wrote 9968 into register 11
Cycle 199: Wrote 9967 into register 11
Cycle 205: Wrote 9966 into register 11
Cycle 211: Wrote 9965 into register 11
Cycle 217: Wrote 9964 into register 11
Cycle 223: Wrote 9963 into register 11
Cycle 229: Wrote 9962 into register 11
Cycle 235: Wrote 9961 into register 11
Cycle 241: Wrote 9960 into register 11
Cycle 247: Wrote 9959 into register 11
Cycle 253: Wrote 9958 into register 11
============== Testing Mode ==============
Reg  0:           0
Reg  1:           1
Reg  2:           0
Reg  3:           0
Reg  4:           0
Reg  5:           0
Reg  6:           0
Reg  7:           0
Reg  8:           0
Reg  9:           0
Reg 10:          20
Reg 11:        9958
Reg 12:           0
Reg 13:           0
Reg 14:           0
Reg 15:           0
Reg 16:           0
Reg 17:           0
Reg 18:           0
Reg 19:           0
Reg 20:           0
Reg 21:           0
Reg 22:           0
Reg 23:           0
Reg 24:           0
Reg 25:           0
Reg 26:           0
Reg 27:           0
Reg 28:           0
Reg 29:           0
Reg 30:           0
Reg 31:           0

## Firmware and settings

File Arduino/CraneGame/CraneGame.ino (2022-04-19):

// Include the AccelStepper Library
#include <AccelStepper.h>

// TODO
// Relay - button as input, which should toggle relay
// Take game active input, which should disable electromagnet and motors. (and send motors to waiting mode?)
// LEDS


// ----- BUTTONS -----
// Input Pins
const int right = 25;
const int left = 27;
const int buttonPin_3_CW = 29;
const int buttonPin_3_CCW = 31;

int FSRpinTL = A12;
int FSRpinTR = A13;
int FSRpinBL = A14;
int FSRpinBR = A15;
int score_pin = 49;

int valueTL = 0;
int valueTR = 0;
int valueBL = 0; 
int valueBR = 0; 
int total_force_analogue = 0;
int total_force_old = 0;
int senVal[] = {0, 0, 0, 0, 0, 0, 0, 0, 0, 0};
int i = 0;
int avg = 0; 


// ----- BUTTONS -----
// Right
int buttonState_right = LOW;             // the current reading from the input pin
int lastButtonState_right = LOW;   // the previous reading from the input pin
int debouncedOutput_right = HIGH;
unsigned long lastDebounceTime_right = 0;  // the last time the output pin was toggled
unsigned long debounceDelay_right = 50;    // the debounce time; increase if the output flickers

// Left
int buttonState_left = LOW;
int lastButtonState_left = LOW;
int debouncedOutput_left = HIGH;
unsigned long lastDebounceTime_left = 0;
unsigned long debounceDelay_left = 50;

// Motor 3 Button CW
int buttonState_3_CW = LOW;
int lastButtonState_3_CW = LOW;
int debouncedOutput_3_CW = HIGH;
unsigned long lastDebounceTime_3_CW = 0;
unsigned long debounceDelay_3_CW = 50;

// Motor 3 Button CCW
int buttonState_3_CCW = LOW;
int lastButtonState_3_CCW = LOW;
int debouncedOutput_3_CCW = HIGH;
unsigned long lastDebounceTime_3_CCW = 0;
unsigned long debounceDelay_3_CCW = 50;

// ----- MOTORS -----
// Define motor interface type
#define motorInterfaceType 1
#define moveDistance 10

const int stepPin_1 = 2;
const int dirPin_1 = 5;
AccelStepper myStepper_1(motorInterfaceType, stepPin_1, dirPin_1);

const int stepPin_2 = 3;
const int dirPin_2 = 6;
AccelStepper myStepper_2(motorInterfaceType, stepPin_2, dirPin_2);

const int stepPin_3 = 4;
const int dirPin_3 = 7;
AccelStepper myStepper_3(motorInterfaceType, stepPin_3, dirPin_3);


void setup() {

  Serial.begin(9600);
  
  pinMode(right, INPUT);
  pinMode(left, INPUT);
  pinMode(buttonPin_3_CW, INPUT);
  pinMode(buttonPin_3_CCW, INPUT);
  pinMode(score_pin, OUTPUT);

  myStepper_1.setCurrentPosition(0);
  myStepper_1.setMaxSpeed(1000);
  myStepper_1.setAcceleration(300);
  myStepper_1.setSpeed(1000);

  myStepper_2.setCurrentPosition(0);
  myStepper_2.setMaxSpeed(1000);
  myStepper_2.setAcceleration(300);
  myStepper_2.setSpeed(1000);

  myStepper_3.setCurrentPosition(0);
  myStepper_3.setMaxSpeed(1000);
  myStepper_3.setAcceleration(300);
  myStepper_3.setSpeed(1000);
}

void loop() {

  // ----- FORCE SENSORS -----
//  total_force_old = total_force_analogue;
//  valueTL = analogRead(FSRpinTL);
//  valueTR = analogRead(FSRpinTR);
//  valueBL = analogRead(FSRpinBL);
//  valueBR = analogRead(FSRpinBR);
//  total_force_analogue = (valueTL+valueTR+valueBL+valueBR);
//
//  if (total_force_analogue == 0) {
//    Serial.println("No pressure");  
//  }
//
//  Serial.print("total force analog: ");
//  Serial.println(total_force_analogue);
//  
//  for (i = 0; i < 10; i = i + 1) {
//    avg += senVal[i];
//  }
//  avg /= 10;
//  Serial.print("avg value: ");
//  Serial.println(avg);
//
//  if(total_force_analogue - avg >= 150){
//    digitalWrite(score_pin, HIGH);
//  }
//
//  senVal[0] = senVal[1];
//  senVal[1] = senVal[2]; 
//  senVal[2] = senVal[3];  
//  senVal[3] = senVal[4];
//  senVal[4] = senVal[5];
//  senVal[5] = senVal[6]; 
//  senVal[6] = senVal[7]; 
//  senVal[7] = senVal[8]; 
//  senVal[8] = senVal[9];
//  senVal[9] = total_force_analogue;


  // ----- DEBOUNCING -----
  // Debounce motor 1 button CW
  int reading_right = digitalRead(right);
  if (reading_right != lastButtonState_right) {
    lastDebounceTime_right = millis();
  }
  if ((millis() - lastDebounceTime_right) > debounceDelay_right) {
    if (reading_right != buttonState_right) {
      buttonState_right = reading_right;
    }
  }
  lastButtonState_right = reading_right;

  // Debounce motor 1 button CCW
  int reading_left = digitalRead(left);
  if (reading_left != lastButtonState_left) {
    lastDebounceTime_left = millis();
  }
  if ((millis() - lastDebounceTime_left) > debounceDelay_left) {
    if (reading_left != buttonState_left) {
      buttonState_left = reading_left;
    }
  }
  lastButtonState_left = reading_left;


  // Debounce motor 3 button CW
  int reading_3_CW = digitalRead(buttonPin_3_CW);
  if (reading_3_CW != lastButtonState_3_CW) {
    lastDebounceTime_3_CW = millis();
  }
  if ((millis() - lastDebounceTime_3_CW) > debounceDelay_3_CW) {
    if (reading_3_CW != buttonState_3_CW) {
      buttonState_3_CW = reading_3_CW;
    }
  }
  lastButtonState_3_CW = reading_3_CW;

  // Debounce motor 3 button CCW
  int reading_3_CCW = digitalRead(buttonPin_3_CCW);
  if (reading_3_CCW != lastButtonState_3_CCW) {
    lastDebounceTime_3_CCW = millis();
  }
  if ((millis() - lastDebounceTime_3_CCW) > debounceDelay_3_CCW) {
    if (reading_3_CCW != buttonState_3_CCW) {
      buttonState_3_CCW = reading_3_CCW;
    }
  }
  lastButtonState_3_CCW = reading_3_CCW;


  // ----- CONTROLLING MOTORS -----
  bool motor_ButtonPressed = (buttonState_right == HIGH) || (buttonState_left == HIGH);
  bool motor_BothButtonsPressed = (buttonState_right == HIGH) && (buttonState_left == HIGH);

  bool motor_3_ButtonPressed = (buttonState_3_CW == HIGH) || (buttonState_3_CCW == HIGH);
  bool motor_3_BothButtonsPressed = (buttonState_3_CW == HIGH) && (buttonState_3_CCW == HIGH);  

  // Don't want both motors moving at the same time
  // For simplicity, will make motor1 have priority
  // Ideally, whatever motor button that was hit last would be running. Could use lastDebounceTime?  
  if (motor_ButtonPressed) {
    // If both buttons pressed, do nothing
    if (motor_BothButtonsPressed) {  
      myStepper_1.move(0);
      myStepper_2.move(0);
    }
    else if (buttonState_right == HIGH) {
      myStepper_1.move(moveDistance);  // Move clockwise
      myStepper_2.move(moveDistance);
    }
    else if (buttonState_left == HIGH) {
      myStepper_1.move(-moveDistance);  // Move clockwise
      myStepper_2.move(-moveDistance);
    }
  } 

  if (motor_3_ButtonPressed) {
    // If both buttons pressed, do nothing
    if (motor_3_BothButtonsPressed) {  
      myStepper_3.move(0);
    }
    else if (buttonState_3_CW == HIGH) {
      myStepper_3.move(moveDistance);  // Move clockwise
    }
    else if (buttonState_3_CCW == HIGH) {
      myStepper_3.move(-moveDistance);  // Move clockwise
    }
  } 


  myStepper_1.run();
  myStepper_2.run();
  myStepper_3.run();
}

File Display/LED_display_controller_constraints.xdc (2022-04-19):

## This file is a general .xdc for the Nexys A7-100T
## To use it in a project:
## - uncomment the lines corresponding to used pins
## - rename the used ports (in each line, after get_ports) according to the top level signal names in the project

## Clock signal
set_property -dict { PACKAGE_PIN E3    IOSTANDARD LVCMOS33 } [get_ports { clock }]; #IO_L12P_T1_MRCC_35 Sch=clk100mhz
create_clock -add -name sys_clk_pin -period 10.00 -waveform {0 5} [get_ports { clock }];


##Switches
set_property -dict { PACKAGE_PIN J15   IOSTANDARD LVCMOS33 } [get_ports { reset }]; #IO_L24N_T3_RS0_15 Sch=sw[0]
#set_property -dict { PACKAGE_PIN L16   IOSTANDARD LVCMOS33 } [get_ports { SW[1] }]; #IO_L3N_T0_DQS_EMCCLK_14 Sch=sw[1]
#set_property -dict { PACKAGE_PIN M13   IOSTANDARD LVCMO S33 } [get_ports { SW[2] }]; #IO_L6N_T0_D08_VREF_14 Sch=sw[2]
#set_property -dict { PACKAGE_PIN R15   IOSTANDARD LVCMOS33 } [get_ports { SW[3] }]; #IO_L13N_T2_MRCC_14 Sch=sw[3]
#set_property -dict { PACKAGE_PIN R17   IOSTANDARD LVCMOS33 } [get_ports { SW[4] }]; #IO_L12N_T1_MRCC_14 Sch=sw[4]
#set_property -dict { PACKAGE_PIN T18   IOSTANDARD LVCMOS33 } [get_ports { SW[5] }]; #IO_L7N_T1_D10_14 Sch=sw[5]
#set_property -dict { PACKAGE_PIN U18   IOSTANDARD LVCMOS33 } [get_ports { SW[6] }]; #IO_L17N_T2_A13_D29_14 Sch=sw[6]
#set_property -dict { PACKAGE_PIN R13   IOSTANDARD LVCMOS33 } [get_ports { SW[7] }]; #IO_L5N_T0_D07_14 Sch=sw[7]
#set_property -dict { PACKAGE_PIN T8    IOSTANDARD LVCMOS18 } [get_ports { SW[8] }]; #IO_L24N_T3_34 Sch=sw[8]
#set_property -dict { PACKAGE_PIN U8    IOSTANDARD LVCMOS18 } [get_ports { SW[9] }]; #IO_25_34 Sch=sw[9]
#set_property -dict { PACKAGE_PIN R16   IOSTANDARD LVCMOS33 } [get_ports { SW[10] }]; #IO_L15P_T2_DQS_RDWR_B_14 Sch=sw[10]
#set_property -dict { PACKAGE_PIN T13   IOSTANDARD LVCMOS33 } [get_ports { SW[11] }]; #IO_L23P_T3_A03_D19_14 Sch=sw[11]
#set_property -dict { PACKAGE_PIN H6    IOSTANDARD LVCMOS33 } [get_ports { SW[12] }]; #IO_L24P_T3_35 Sch=sw[12]
#set_property -dict { PACKAGE_PIN U12   IOSTANDARD LVCMOS33 } [get_ports { SW[13] }]; #IO_L20P_T3_A08_D24_14 Sch=sw[13]
#set_property -dict { PACKAGE_PIN U11   IOSTANDARD LVCMOS33 } [get_ports { SW[14] }]; #IO_L19N_T3_A09_D25_VREF_14 Sch=sw[14]
#set_property -dict { PACKAGE_PIN V10   IOSTANDARD LVCMOS33 } [get_ports { SW[15] }]; #IO_L21P_T3_DQS_14 Sch=sw[15]

## LEDs
#set_property -dict { PACKAGE_PIN H17   IOSTANDARD LVCMOS33 } [get_ports { LED[0] }]; #IO_L18P_T2_A24_15 Sch=led[0]
#set_property -dict { PACKAGE_PIN K15   IOSTANDARD LVCMOS33 } [get_ports { LED[1] }]; #IO_L24P_T3_RS1_15 Sch=led[1]
#set_property -dict { PACKAGE_PIN J13   IOSTANDARD LVCMOS33 } [get_ports { LED[2] }]; #IO_L17N_T2_A25_15 Sch=led[2]
#set_property -dict { PACKAGE_PIN N14   IOSTANDARD LVCMOS33 } [get_ports { LED[3] }]; #IO_L8P_T1_D11_14 Sch=led[3]
#set_property -dict { PACKAGE_PIN R18   IOSTANDARD LVCMOS33 } [get_ports { LED[4] }]; #IO_L7P_T1_D09_14 Sch=led[4]
#set_property -dict { PACKAGE_PIN V17   IOSTANDARD LVCMOS33 } [get_ports { LED[5] }]; #IO_L18N_T2_A11_D27_14 Sch=led[5]
#set_property -dict { PACKAGE_PIN U17   IOSTANDARD LVCMOS33 } [get_ports { LED[6] }]; #IO_L17P_T2_A14_D30_14 Sch=led[6]
#set_property -dict { PACKAGE_PIN U16   IOSTANDARD LVCMOS33 } [get_ports { LED[7] }]; #IO_L18P_T2_A12_D28_14 Sch=led[7]
#set_property -dict { PACKAGE_PIN V16   IOSTANDARD LVCMOS33 } [get_ports { LED[8] }]; #IO_L16N_T2_A15_D31_14 Sch=led[8]
#set_property -dict { PACKAGE_PIN T15   IOSTANDARD LVCMOS33 } [get_ports { LED[9] }]; #IO_L14N_T2_SRCC_14 Sch=led[9]
#set_property -dict { PACKAGE_PIN U14   IOSTANDARD LVCMOS33 } [get_ports { LED[10] }]; #IO_L22P_T3_A05_D21_14 Sch=led[10]
#set_property -dict { PACKAGE_PIN T16   IOSTANDARD LVCMOS33 } [get_ports { LED[11] }]; #IO_L15N_T2_DQS_DOUT_CSO_B_14 Sch=led[11]
#set_property -dict { PACKAGE_PIN V15   IOSTANDARD LVCMOS33 } [get_ports { LED[12] }]; #IO_L16P_T2_CSI_B_14 Sch=led[12]
#set_property -dict { PACKAGE_PIN V14   IOSTANDARD LVCMOS33 } [get_ports { LED[13] }]; #IO_L22N_T3_A04_D20_14 Sch=led[13]
#set_property -dict { PACKAGE_PIN V12   IOSTANDARD LVCMOS33 } [get_ports { LED[14] }]; #IO_L20N_T3_A07_D23_14 Sch=led[14]
#set_property -dict { PACKAGE_PIN V11   IOSTANDARD LVCMOS33 } [get_ports { LED[15] }]; #IO_L21N_T3_DQS_A06_D22_14 Sch=led[15]

## RGB LEDs
#set_property -dict { PACKAGE_PIN R12   IOSTANDARD LVCMOS33 } [get_ports { LED16_B }]; #IO_L5P_T0_D06_14 Sch=led16_b
#set_property -dict { PACKAGE_PIN M16   IOSTANDARD LVCMOS33 } [get_ports { LED16_G }]; #IO_L10P_T1_D14_14 Sch=led16_g
#set_property -dict { PACKAGE_PIN N15   IOSTANDARD LVCMOS33 } [get_ports { LED16_R }]; #IO_L11P_T1_SRCC_14 Sch=led16_r
#set_property -dict { PACKAGE_PIN G14   IOSTANDARD LVCMOS33 } [get_ports { LED17_B }]; #IO_L15N_T2_DQS_ADV_B_15 Sch=led17_b
#set_property -dict { PACKAGE_PIN R11   IOSTANDARD LVCMOS33 } [get_ports { LED17_G }]; #IO_0_14 Sch=led17_g
#set_property -dict { PACKAGE_PIN N16   IOSTANDARD LVCMOS33 } [get_ports { LED17_R }]; #IO_L11N_T1_SRCC_14 Sch=led17_r
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

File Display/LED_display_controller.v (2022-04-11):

module LED_display_controller(
    input clock_100Mhz,  // 100 Mhz clock source on Basys 3 FPGA
    input reset,  // reset
    input [15:0] displayed_number1,
    input [15:0] displayed_number2,
    output reg [7:0] anode_activate,  // anode signals of the 7-segment LED display
    output reg [7:0] LED_out  // cathode patterns of the 7-segment LED display
    );
    
    reg [3:0] LED_BCD;
    reg [19:0] refresh_counter; // 20-bit for creating 10.5ms refresh period or 380Hz refresh rate
             // the first 3 MSB bits for creating 8 LED-activating signals with 10.5ms refresh period, 1.3 digit period
    wire [2:0] LED_activating_counter;  // Counts from 0 to 7, activating each LED one at a time
    
    
    always @(posedge clock_100Mhz or posedge reset)
    begin 
        if(reset==1)
            refresh_counter <= 0;
        else
            refresh_counter <= refresh_counter + 1;
    end 
    assign LED_activating_counter = refresh_counter[19:17];


    // anode activating signals for 8 LEDs, digit period of 1.3ms
    // decoder to generate anode signals 
    always @(*)
    begin
        case(LED_activating_counter)
            3'b000: begin
                anode_activate = 8'b01111111; 
                LED_BCD = displayed_number1 / 1000;
                end
            3'b001: begin
                anode_activate = 8'b10111111; 
                LED_BCD = (displayed_number1 % 1000) / 100;
                end
            3'b010: begin
                anode_activate = 8'b11011111; 
                LED_BCD = (displayed_number1 % 100) / 10;
                end
            3'b011: begin
                anode_activate = 8'b11101111; 
                LED_BCD = (displayed_number1 % 10); 
                end
            3'b100: begin
                anode_activate = 8'b11110111; 
                LED_BCD = displayed_number2 / 1000;
                end
            3'b101: begin
                anode_activate = 8'b11111011; 
                LED_BCD = (displayed_number2 % 1000) / 100;
                end
            3'b110: begin
                anode_activate = 8'b11111101; 
                LED_BCD = (displayed_number2 % 100) / 10;
                end
            3'b111: begin
                anode_activate = 8'b11111110; 
                LED_BCD = (displayed_number2 % 10); 
                end
        endcase
    end


    // Cathode patterns of the 7-segment LED display 
    always @(*)
    begin
        case(LED_BCD)
        4'b0000: LED_out = 8'b00000011; // "0"     
        4'b0001: LED_out = 8'b10011111; // "1" 
        4'b0010: LED_out = 8'b00100101; // "2" 
        4'b0011: LED_out = 8'b00001101; // "3" 
        4'b0100: LED_out = 8'b10011001; // "4" 
        4'b0101: LED_out = 8'b01001001; // "5" 
        4'b0110: LED_out = 8'b01000001; // "6" 
        4'b0111: LED_out = 8'b00011111; // "7" 
        4'b1000: LED_out = 8'b00000001; // "8"     
        4'b1001: LED_out = 8'b00001001; // "9" 
        default: LED_out = 8'b00000011; // "0"
        endcase
    end
 endmodule

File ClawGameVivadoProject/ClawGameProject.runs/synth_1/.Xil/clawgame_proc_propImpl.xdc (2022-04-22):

set_property SRC_FILE_INFO {cfile:C:/Users/tyler/Documents/Spring2022/ECE350/final-project-team-25/clawgame.xdc rfile:../../../../clawgame.xdc id:1} [current_design]
set_property src_info {type:XDC file:1 line:7 export:INPUT save:INPUT read:READ} [current_design]
set_property -dict { PACKAGE_PIN E3    IOSTANDARD LVCMOS33 } [get_ports { clock }]; #IO_L12P_T1_MRCC_35 Sch=clk100mhz
set_property src_info {type:XDC file:1 line:56 export:INPUT save:INPUT read:READ} [current_design]
set_property -dict { PACKAGE_PIN T10   IOSTANDARD LVCMOS33 } [get_ports { LED_out[7] }]; #IO_L24N_T3_A00_D16_14 Sch=ca
set_property src_info {type:XDC file:1 line:57 export:INPUT save:INPUT read:READ} [current_design]
set_property -dict { PACKAGE_PIN R10   IOSTANDARD LVCMOS33 } [get_ports { LED_out[6] }]; #IO_25_14 Sch=cb
set_property src_info {type:XDC file:1 line:58 export:INPUT save:INPUT read:READ} [current_design]
set_property -dict { PACKAGE_PIN K16   IOSTANDARD LVCMOS33 } [get_ports { LED_out[5] }]; #IO_25_15 Sch=cc
set_property src_info {type:XDC file:1 line:59 export:INPUT save:INPUT read:READ} [current_design]
set_property -dict { PACKAGE_PIN K13   IOSTANDARD LVCMOS33 } [get_ports { LED_out[4] }]; #IO_L17P_T2_A26_15 Sch=cd
set_property src_info {type:XDC file:1 line:60 export:INPUT save:INPUT read:READ} [current_design]
set_property -dict { PACKAGE_PIN P15   IOSTANDARD LVCMOS33 } [get_ports { LED_out[3] }]; #IO_L13P_T2_MRCC_14 Sch=ce
set_property src_info {type:XDC file:1 line:61 export:INPUT save:INPUT read:READ} [current_design]
set_property -dict { PACKAGE_PIN T11   IOSTANDARD LVCMOS33 } [get_ports { LED_out[2] }]; #IO_L19P_T3_A10_D26_14 Sch=cf
set_property src_info {type:XDC file:1 line:62 export:INPUT save:INPUT read:READ} [current_design]
set_property -dict { PACKAGE_PIN L18   IOSTANDARD LVCMOS33 } [get_ports { LED_out[1] }]; #IO_L4P_T0_D04_14 Sch=cg
set_property src_info {type:XDC file:1 line:63 export:INPUT save:INPUT read:READ} [current_design]
set_property -dict { PACKAGE_PIN H15   IOSTANDARD LVCMOS33 } [get_ports { LED_out[0] }]; #IO_L19N_T3_A21_VREF_15 Sch=dp
set_property src_info {type:XDC file:1 line:65 export:INPUT save:INPUT read:READ} [current_design]
set_property -dict { PACKAGE_PIN J17   IOSTANDARD LVCMOS33 } [get_ports { anode_activate[0] }]; #IO_L23P_T3_FOE_B_15 Sch=an[0]
set_property src_info {type:XDC file:1 line:66 export:INPUT save:INPUT read:READ} [current_design]
set_property -dict { PACKAGE_PIN J18   IOSTANDARD LVCMOS33 } [get_ports { anode_activate[1] }]; #IO_L23N_T3_FWE_B_15 Sch=an[1]
set_property src_info {type:XDC file:1 line:67 export:INPUT save:INPUT read:READ} [current_design]
set_property -dict { PACKAGE_PIN T9    IOSTANDARD LVCMOS33 } [get_ports { anode_activate[2] }]; #IO_L24P_T3_A01_D17_14 Sch=an[2]
set_property src_info {type:XDC file:1 line:68 export:INPUT save:INPUT read:READ} [current_design]
set_property -dict { PACKAGE_PIN J14   IOSTANDARD LVCMOS33 } [get_ports { anode_activate[3] }]; #IO_L19P_T3_A22_15 Sch=an[3]
set_property src_info {type:XDC file:1 line:69 export:INPUT save:INPUT read:READ} [current_design]
set_property -dict { PACKAGE_PIN P14   IOSTANDARD LVCMOS33 } [get_ports { anode_activate[4] }]; #IO_L8N_T1_D12_14 Sch=an[4]
set_property src_info {type:XDC file:1 line:70 export:INPUT save:INPUT read:READ} [current_design]
set_property -dict { PACKAGE_PIN T14   IOSTANDARD LVCMOS33 } [get_ports { anode_activate[5] }]; #IO_L14P_T2_SRCC_14 Sch=an[5]
set_property src_info {type:XDC file:1 line:71 export:INPUT save:INPUT read:READ} [current_design]
set_property -dict { PACKAGE_PIN K2    IOSTANDARD LVCMOS33 } [get_ports { anode_activate[6] }]; #IO_L23P_T3_35 Sch=an[6]
set_property src_info {type:XDC file:1 line:72 export:INPUT save:INPUT read:READ} [current_design]
set_property -dict { PACKAGE_PIN U13   IOSTANDARD LVCMOS33 } [get_ports { anode_activate[7] }]; #IO_L23N_T3_A02_D18_14 Sch=an[7]
set_property src_info {type:XDC file:1 line:85 export:INPUT save:INPUT read:READ} [current_design]
set_property -dict { PACKAGE_PIN C17   IOSTANDARD LVCMOS33 } [get_ports { game_active }]; #IO_L20N_T3_A19_15 Sch=ja[1]
set_property src_info {type:XDC file:1 line:95 export:INPUT save:INPUT read:READ} [current_design]
set_property -dict { PACKAGE_PIN D14   IOSTANDARD LVCMOS33 } [get_ports { increment_score }]; #IO_L1P_T0_AD0P_15 Sch=jb[1]
set_property src_info {type:XDC file:1 line:102 export:INPUT save:INPUT read:READ} [current_design]
set_property -dict { PACKAGE_PIN H16   IOSTANDARD LVCMOS33 } [get_ports { reset }]; #IO_L13P_T2_MRCC_15 Sch=jb[10]

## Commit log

2022-04-11 Add arduino code for motors and relay test
2022-04-11 Add draft of assembly code and custom commands
    [custom_commands.csv]
2022-04-11 Create Display directory with the timer and display controller
2022-04-11 Countdown timer and score is working on the seven segment display
2022-04-11 FPGA 3.3V works as input to digital logic arduino pins
2022-04-11 Have FPGA output game_active signal, which is set off when reset or time has counted down
    [LED_display_controller_constraints.xdc]
2022-04-19 Upload Load Plate four input file
2022-04-19 Status as of 4/19 3pm
    [Basic Wheel v1.stl, Basic Wheel v2.stl, Basic Wheel v3.stl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]
2022-04-20 Working timer and score counter, but doesn't initialize timer to correct value
    [CraneGameMotors.ino, clawgame_proc_propImpl.xdc]
2022-04-20 Timer initialized correctly
2022-04-20 Working yay
    [Load Plate v9.stl]
